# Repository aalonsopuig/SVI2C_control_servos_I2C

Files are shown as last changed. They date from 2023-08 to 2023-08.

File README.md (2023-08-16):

<html>

<head>
<meta http-equiv="Content-Language" content="es">
<meta name="GENERATOR" content="Microsoft FrontPage 4.0">
<meta name="ProgId" content="FrontPage.Editor.Document">
</head>

<font size="4"><b><i>Diseño de un módulo para control de
      8 servos y 5 canales analógicos por bus I<sup>2</sup>C</i></b></font>
      <p>Por Alejandro Alonso Puig<br>
      Octubre 2.003<br>
<hr>
<p align="justify"><br>
El presente repositorio incluye no solo los programas y esquemático del circuito en Eagle, 
sino también el informe técnico que describe el diseño, tanto desde el punto de vista
electrónico, como informático de un placa para control por bus I<sup>2</sup>C
de 8 servos estándar de radiocontrol y 5 entradas analógicas (Conversión
analógica/digital). Las características principales del módulo presentado son
las siguientes:&nbsp;</p>
<ul>
  <li>
    <p align="justify">Actúa como Slave permitiendo seleccionar mediante
    switches dip la dirección que utilizará en la red I<sup>2</sup>C.&nbsp;</li>
  <li>
    <p align="justify">Se puede establecer mediante bus I<sup>2</sup>C tanto la
    posición deseada de cada servo, como el sentido de giro y el Offset.&nbsp;</li>
  <li>
    <p align="justify">Se puede leer por bus I<sup>2</sup>C el valor digital (8
    bits) correspondiente a cualquiera de las 5 entradas analógicas de las que
    dispone.&nbsp;</li>
  <li>
    <p align="justify">Implementa un microcontrolador PIC 16F876 programado en ensamblador, lo que hace el código muy rápido.&nbsp;</li>
</ul>
<p align="justify">&nbsp;</p>
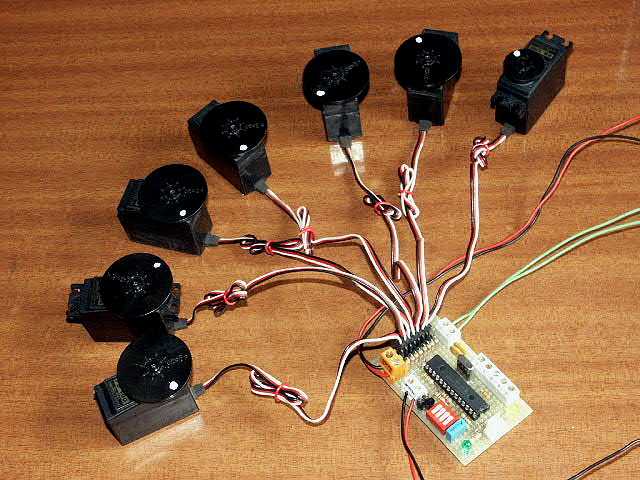
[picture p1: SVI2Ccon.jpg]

<p align="justify">La ventaja que se obtiene con este tipo de módulos es
precisamente el control por bus I<sup>2</sup>C que permite tener varios módulos
de este tipo ventaja que se obtiene con este tipo de módulos es precisamente el
control por bus I<sup>2</sup>C que permite tener varios módulos de este tipo
conectados al mismo bus. De esta manera pueden controlarse gran cantidad de
servos desde un controlador principal sin apenas sobrecarga en el mismo.
Adicionalmente se tiene medida de valores analógicos, muy útil para
determinado tipo de sensores.</p>
<p><b>Nota</b>: Master y Slave han de estar conectados mediante tres hilos:
Masa, SCL y SDA. El módulo presentado incluye las resistencias de PullUp, por
lo que no es necesario añadirlas.</p>
<p>

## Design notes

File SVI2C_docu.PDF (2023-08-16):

mundobot.com | Alejandro Alonso Puig

# Diseño de un módulo para control de 8 servos y 5 canales analógicos por bus I²

C

# Alejandro Alonso Puig – mundobot.com Octubre 2003

## Comandos I²

# Introducción

El siguiente informe técnico describe el diseño,

## tanto desde el punto de vista electrónico, como informático de un placa para control por bus I²

C

## de 8 servos estándar de radiocontrol y 5 entradas

analógicas (Conversión analógica/digital).

## Las características principales del módulo presentado son las siguientes:

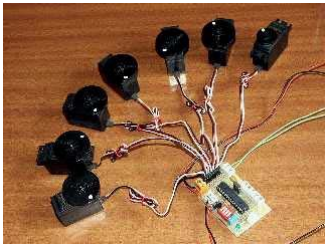
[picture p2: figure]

## - Actúa como Slave permitiendo seleccionar mediante switches dip la dirección que utilizará en la red I²

C.

## - Se puede establecer mediante bus I² C tanto la posición deseada de cada servo, como el

sentido de giro y el Offset.

## - Se puede leer por bus I² C el valor digital (8 bits) correspondiente a cualquiera de las 5

entradas analógicas de las que dispone..

## La ventaja que se obtiene con este tipo de módulos es precisamente el control por bus I²

C

## que permite tener varios módulos de este tipo

## conectados al mismo bus. De esta manera pueden controlarse gran cantidad de servos desde un controlador principal sin apenas sobrecarga en el mismo. Adicionalmente se tiene medida de valores analógicos, muy útil para determinado tipo de

sensores.

# Diseño Electrónico

## El módulo está compuesto básicamente por en un microcontrolador PIC 16F876 de Microchip

funcionando a 4Mhz.

## Este microcontrolador posee un módulo MSSP que permite el control de las comunicaciones I²

C

## por Hardware. Se utilizan los pines SCL (RC3) y SDA (RC4) conectados a resistencias Pull-Up de 10KΩ para las comunicaciones I²

C.

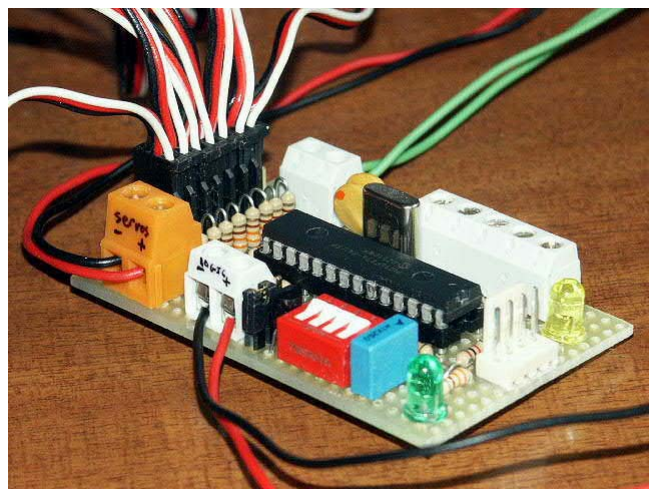
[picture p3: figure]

## Adicionalmente posee un grupo de cinco conversores analógico digitales (A/D) que pueden

soportar entradas analógicas entre 0 y 5 voltios.

## Los valores analógicos serán relativos a la masa del circuito, por lo que la masa del elemento cuya señal analógica se quiera medir deberá estar

conectada a la masa del modulo que presentamos.

## Existen 4 entradas (RB2-RB5) conectadas a un switch-dip cuádruple. Solo las dos inferiores (RB2, RB3) son utilizadas por el firmware actual

## y permitirán seleccionar diferentes direcciones

I

2

## C para evitar coincidencia de direccionamiento con otros dispositivos (entre 01110000 [0x70] y

01110110 [0x76]).

Tiene doble entrada de alimentación, una para los servos y otra para la lógica. Utilizar doble alimentación no es obligatorio, aunque si es recomendable para evitar interferencias en el funcionamiento de la lógica. En cualquier caso el módulo incluye un regulador de tensión a 5 voltios (7805) que puede ser activado o desactivado mediante jumper, según se vaya a

alimentar el circuito con 5 voltios o más.

## Obviamente la masa de ambas tomas de

alimentación es común.

## Finalmente los pines MCLR, RB6 y RB7 se han llevado junto con la masa a un conector cuádruple con el fin de permitir la programación del chip

una vez montado en placa (Programación ICP).

## Las salidas para el control del los servos incluyen resistencias de 330Ω para prevenir daños en el microcontrolador en caso de exceso de consumo

en el circuito interno de los servos.

## El circuito no está protegido en caso de conectar la alimentación incorrectamente, por lo que se ha

de prestar atención a la polaridad.

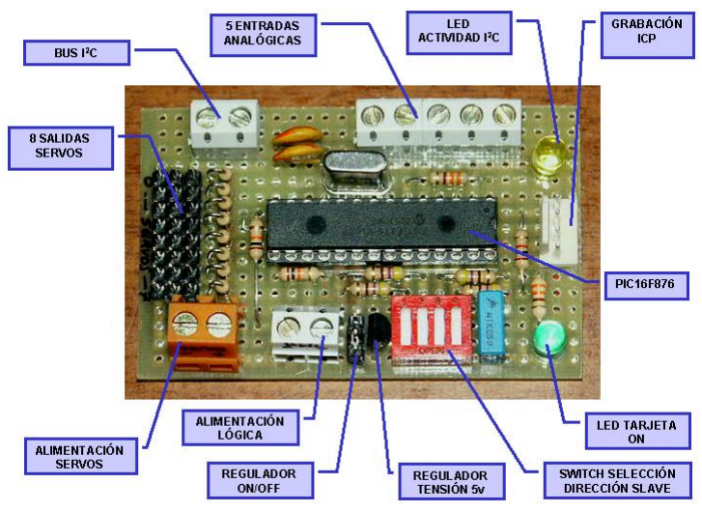
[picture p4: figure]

El esquema electrónico completo se muestra a continuación.

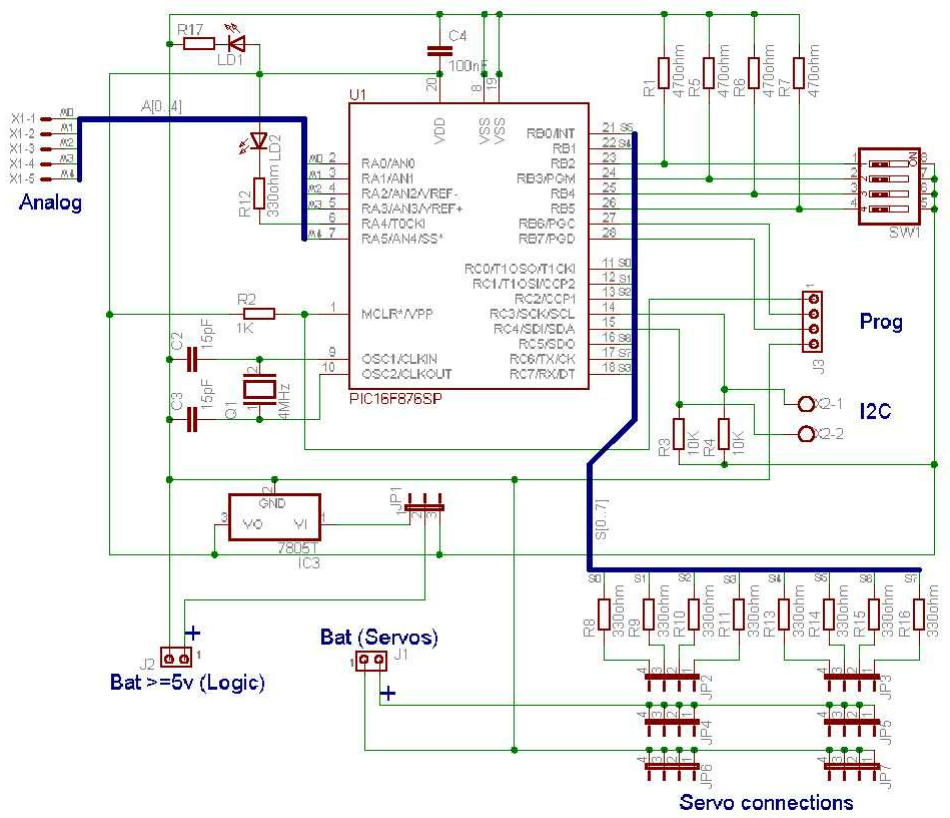
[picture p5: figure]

# Diseño del software

## El software ha sido desarrollado en ensamblador

para PIC16F876.

## El módulo está configurado para producir una interrupción cada vez que se desborda el timer TMR0 o cada vez que se produce un evento I²

C.

## Al atender dicha interrupción verifica cual de los dos tipos es y actúa en consecuencia:

## 9 El TMR0 se configura con un valor adecuado para que se desborde cada 20msg, que es el tiempo en el que se ha de refrescar el valor PWM enviado a los

servos. | Cuando | se | produce | una

## interrupción de este tipo, se atienden los 8 servos secuencialmente, vigilando asimismo si se produce simultáneamente un evento I² C. En caso de producirse, se forzará la parada de la señal de reloj I²

| | | | C

## para que el Master no envíe más información hasta que se tenga tiempo de atender el evento que ha llegado. Así se

impiden overflows.

## 9 Si el evento que ha producido la interrupción es I² C, se atenderá en la rutina “SSP_Handler”, que verificará la adecuada llegada de tramas y se ocupará de actualizar o leer una serie de registros de los que hablaremos más adelante y que serán los responsables del funcionamiento

del módulo.

# Registros

## El módulo contiene una serie de registros que pueden ser accedidos desde un Master por I²

| | | | C.
Algunos de estos registros son solo de lectura, mientras que otros son de escritura.

## Mediante el manejo de estos registros se obtiene toda la funcionalidad del módulo. A continuación describimos dichos registros:

## - Modo: Este registro permite al Master especificar el modo de funcionamiento de cada servo: Normal (giro normal) y Reverse (sentido inverso)

## Cada bit representa un servo. Así por ejemplo, si Modo es 10010100, los servos 0, 1, 3, 5 y 6 girarán en sentido normal y los servos 2, 4 y 7 funcionarán en sentido

inverso.

## Por defecto este registro vale 0, con lo que

todos los servos giran en sentido normal.

## - Offset: Es un registro de solo escritura cuyo valor por defecto es 70. Permite

ajustar la posición cero del servo. Es decir,

## debido a que cada modelo de servo tiene unas características diferentes, la posición cero de dos servos diferentes puede darse en diferentes Duty Cycles (Anchura del pulso positivo). Por ejemplo en un servo

se puede dar con un Duty Cycle de 1msg,

mientras que en otro se puede dar con un Duty Cycle de 400µsg. Por ello ha de ajustarse el Offset a las características del servo. Ha de tenerse en cuenta que una variación de una unidad en el Offset implica una variación de 5µsg en el Duty Cycle. Asimismo ha de tenerse en cuenta que el valor del Duty Cycle vendrá dado en µsg por la siguiente fórmula en este módulo:

## Duty Cycle = 10 + 5xOffset + 8xPosic

## De esta manera, para la posición 0, el Offset será:

5

## −10 = DutyCycle Offset

## Así, para un Duty Cycle de 1msg (1000µsg) en la posición 0, el Offset habrá de ser 198

## - Posic: Es un registro de solo escritura cuyo valor por defecto es 0. Indica la

posición que se desea que tenga el servo. El límite depende del modelo de servo.

Básicamente ha de tenerse en cuenta que un incremento de una unidad en este valor implica un incremento de 8 µsg en el Duty Cycle. Según el valor del Offset de un servo y del valor de Posic, se tendrá un Duty Cycle concreto según la fórmula que se mostró antes. Por ejemplo para un Offset de valor 70 (valor por defecto) y un valor de Posic de 220 generaría una señal

PWM de Duty Cycle = 2.120µsg.

## Por tanto se tiene que los valores límites de Duty Cycle que se pueden conseguir con este módulo varían desde 10µsg

(Offset=0, | Posic=0) | a | 3.325µsg

## (Offset=255, Posic=255)

Los valores son muy extremos, por lo que hay que tener cuidado en su asignación para no dañar el servo. En caso de no conocerse los límites de Duty Cycle de un servo puede procederse de la siguiente manera: Establecer para un servo concreto desde el Master un valor de Posic=0 y un Offset=198. Esto generará un PWM de Duty Cycle = 1000µsg, valor aceptado por cualquier servo comercial. Si se observa que el eje del servo está lejos de su posición de límite físico, se irá reduciendo el valor del Duty Cycle hasta que el eje esté cerca del límite físico. No ha de llegar en ningún momento al límite físico ya que podría dañar el mecanismo de engranajes del servo. Una vez establecido el valor de Offset, se puede ir incrementando progresivamente el valor de Posic hasta que el eje casi llegue a su otro límite físico. Con esto ya se ha conseguido saber

## el valor que ha de tener Offset y los valores límites de Posic

- Analog: Es un registro de solo lectura.

## Indica el valor digital de la conversión A/D de una entrada analógica concreta. La resolución usada en la conversión A/D es de 8 bits, es decir que lo mínimo

detectable son variaciones de 19,5mV.

- Versión: Indica la versión del firmware. Es un registro de solo lectura.

# Comandos I²

C

## Básicamente las órdenes que llegarán del Master al Slave serán de lectura y/o escritura en los

registros mencionados anteriormente.

## En la primera trama se indica el número de registro al que se quiere acceder, bien sea para lectura o escritura. Dicha numeración es la siguiente:

## 1. Registro de Modo 2. Offset servo 3. Posición servo 4. Conversor A/D 5. No usado 6. No usado

7. Revisión Firmware.

## En la segunda trama se indica el número de dispositivo al que nos referimos (número de servo o número de entrada analógica)

## Si estamos escribiendo un registro, en la tercera trama irá el valor que escribimos. Si por el contrario estamos accediendo en modo lectura, se

enviará orden de solicitud del valor del registro.

## Por ejemplo, si se quiere ordenar que el servo número 0 tenga un Offset de 92, habría que enviar un bloque con cuatro bytes:

## 9 Dirección Slave en modo escritura (si no se cambian los switches será 112

(01110000))

## 9 Nº Registro a acceder (Offset=2) 9 Nº Dispositivo a acceder (Servo0 --> 0) 9 Valor Registro: 92

## Si lo que se quiere por ejemplo es leer el valor de la entrada analógica número 3, se enviaría un primer bloque con 3 bytes:

## 9 Dirección Slave en modo escritura (si no se cambian los switches será 112

(01110000))

## 9 Nº Registro a acceder (A/D=4) 9 Nº Dispositivo a acceder (Entrada nº 3 -->

3)

## Tras esto se enviaría un segundo bloque con un byte:

## 9 Dirección Slave en modo lectura (si no se

cambian | los | switches | será | 113
(01110001))

## .. y se recibirá del Slave un byte correspondiente

al dato solicitado.

## A continuación se muestra el formato de los comandos I² C utilizados para el intercambio de datos entre Master y Slave a nivel de lógica

digital.

## Escritura registro

## En caso de querer escribir en un registro, se enviará desde el Master al Slave un solo bloque de datos con cuatro bytes (Dirección Slave en modo escritura, nº registro, nº dispositivo, valor

registro).

## Tomando el ejemplo anterior de establecimiento de un valor 92 para el Offset, la representación de la transmisión a nivel de lógica digital sería como sigue:

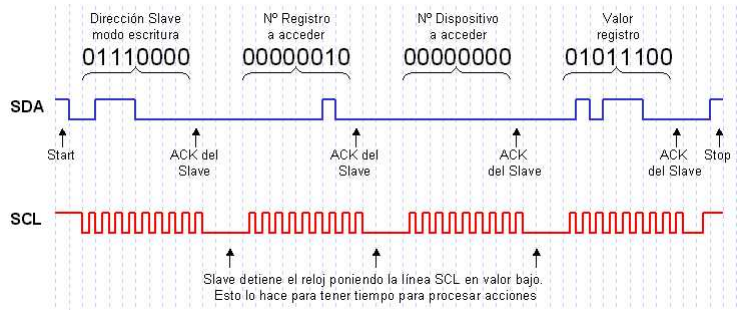
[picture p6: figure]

## Lectura Registro

## En caso de querer leer de un registro, se enviará desde el Master al Slave un bloque con tres bytes (Dirección Slave en modo escritura, nº registro, nº dispositivo) y otro bloque con un byte (Dirección

## Slave en modo lectura). El Slave contestará con otro bloque de un byte (valor de registro solicitado)

## Tomando el ejemplo anterior de lectura de un valor del conversor A/D, la representación de la

## transmisión a nivel de lógica digital sería como sigue:

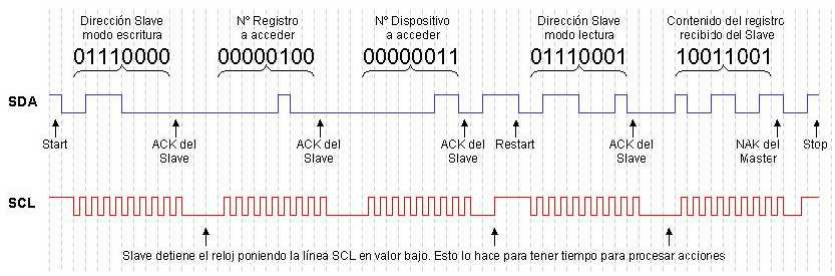
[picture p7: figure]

# Cuerpo del programa

Básicamente el funcionamiento del programa consiste en un bucle en el que mientras no se produzca una interrupción por evento I² C o por desbordamiento del TMR0, Va haciendo conversiones A/D de sus 5 entradas analógicas y dejándolas en variables para que en caso de ser solicitadas por I² C pueda entregar los valores de

## forma inmediata. Esto se hace porque la toma de un valor analógico y su conversión a un dato digital toma cierto tiempo. Teniendo siempre los

valores ya convertidos, se agiliza la transmisión.

# Código fuente

A continuación se incluye el código fuente del módulo comentado. Incluye comentarios que aclararán su funcionamiento.

; SvI2C02
; Programa para control de servos y entradas analógicas por bus I2C ; Por: Alejandro Alonso Puig
; Fecha: 11/10/2003
; Controlador: 16F876 4Mhz
; Función:
; Control de hasta 8 servos y 5 entradas analógicas.
; Dispone de las siguientes características:
; -Valores de posicionamiento (0 a 255)
; -Permite funcionar a cada servo en modo normal o reverse
; -Permite establecer un Offset por servo para fijar posición inicial ; -Switches dip para especificar la dirección i2c que se utilizará
; -Conversión A/D de 5 entradas analógicas
;

; La anchura de flanco alto (Duty Cycle) enviada a cada servo vendrá dada en usg por la formula ; Duty Cycle en usg = 10 + 5xOffset + 8xPosic en caso de funcionamiento normal y
; Duty Cycle en usg = 10 + 5xOffset + 8x(255-Posic) en caso de funcionamiento reverse
list | p=16F876
include | "P16F876.INC"

;Definición de macros

#define Version | d'02' | ;Versión del programa

;Puertos
#define Servo0 PORTC,0 | ; Servo nº0

#define Servo1 PORTC,1 | ; Servo nº1

#define Servo2 PORTC,2 | ; Servo nº2

#define Servo3 PORTC,7 | ; Servo nº3

#define Servo4 PORTB,1 | ; Servo nº4

#define Servo5 PORTB,0 | ; Servo nº5

#define Servo6 PORTC,5 | ; Servo nº6

#define Servo7 PORTC,6 | ; Servo nº7

#define S0 | .0 | ;Referencia al servo 0 en palabras de estado

#define S1 | .1 | ;Referencia al servo 1 en palabras de estado

#define S2 | .2 | ;Referencia al servo 2 en palabras de estado

#define S3 | .3 | ;Referencia al servo 3 en palabras de estado

#define S4 | .4 | ;Referencia al servo 4 en palabras de estado

#define S5 | .5 | ;Referencia al servo 5 en palabras de estado

#define S6 | .6 | ;Referencia al servo 6 en palabras de estado

#define S7 | .7 | ;Referencia al servo 7 en palabras de estado

#define Led | PORTA,4 | ;Led de actividad I2C

;Definición de variables

cblock 0x20

;Variables para control de servos
DispNo | ;Numero de dispositivo accedido desde I2C (Servo, pto Analog)
Posic | ;Variable Posicion Servo para cálculo retardo
Posic0 | ;Posicion Servo nº0 (0 a 255)
Posic1 | ;Posicion Servo nº1 (0 a 255)
Posic2 | ;Posicion Servo nº2 (0 a 255)
Posic3 | ;Posicion Servo nº3 (0 a 255)
Posic4 | ;Posicion Servo nº4 (0 a 255)
Posic5 | ;Posicion Servo nº5 (0 a 255)
Posic6 | ;Posicion Servo nº6 (0 a 255)
Posic7 | ;Posicion Servo nº7 (0 a 255)

;Offsets
;El valor de Offset permite establecer la posición inicial de cada en función ;de la anchura del pulso activo en microsegundos. El cálculo se hace mediante ;la fórmula Offset=(T-10)/5, donde T es la anchura del pulso activo en usg ;Se utiliza para dos funciones: Ajustar varios servos para que sus ejes estén ;colocados físicamente en la misma posición cero, adaptando los
;offsets de cada servo. También se utiliza para aprovechar al máximo el giro ;posible del eje, que varia para cada marca y modelo.
;Por ejemplo, si queremos establecer que el valor de 0 implique un pulso ;activo de una anchura de 1000usg, el offset será (1000-10)/5=198
Offset0 | ;Offset Servo nº0
Offset1 | ;Offset Servo nº1
Offset2 | ;Offset Servo nº2
Offset3 | ;Offset Servo nº3
Offset4 | ;Offset Servo nº4
Offset5 | ;Offset Servo nº5
Offset6 | ;Offset Servo nº6
Offset7 | ;Offset Servo nº7
Offset | ;Valor Offset servo
Modo | ;Palabra de estado que indica en cada bit que servo girará a la inversa
APort | ;Puerto analógico a medir
APortTmp | ;Variable temporal utilizada en la medición
Analog | ;Valor analógico medido

Analog0 | ;Valor analógico puerto 0
Analog1 | ;Valor analógico puerto 1
Analog2 | ;Valor analógico puerto 2
Analog3 | ;Valor analógico puerto 3
Analog4 | ;Valor analógico puerto 4
PDel0 | ;Usada en retardos
ADel0 | ;Usada en retardos
BDel0 | ;Usada en retardos
BDel1 | ;Usada en retardos
BDel2 | ;Usada en retardos
Pausa | ;Usada en para hacer pausas con subr "HacerTiempo"
Temp | ;Variable Temporal para usos puntuales en cálculos
Temp2 | ;Variable Temporal para usos puntuales en cálculos
Temp3 | ;Variable Temporal para usos puntuales en cálculos
BkStatus | ;Backup del registro STATUS
BkW | ;Backup W
BkStatus2 | ;Backup del registro STATUS (Interrupciones)
BkW2 | ;Backup W (Interrupciones)
DirNodo | ;Dirección I2C de este slave (4 posibles direcciones segun switches dip)
MensajeIn | ;Contendrá el dato recibido por I2C del master
MensajeOut | ;Contendrá el dato a enviar por I2C al master
Registro | ;Registro accedido por i2c:
; | 1: Registro de Modo. Normal o Reverse servo
; | 2: Offset servo
; | 3: Posición servo
; | 4: Valor puerto analógico
; | 5: No usado
; | 6: No usado
; | 7: Revisión Firmware. "Version"
StatI2C | ;Registro intermedio para identificar el estado i2c:
; | 0: Si On --> llegó nº Registro
; | 1: Si On --> llegó nº Dispositivo al que se referirá el registro
endc | ;Fin de definiciones
org | 0
goto | INICIO
org | 5

;-------------------------------------------------------------------------------
Interrupcion | ;RUTINA DE INTERRUPCIÓN. Activa flancos segun valor de variables
| ;de Posicion (Servos) y trata eventos I2C
;-------------------------------------------------------------------------------

;Guardamos copia de algunos registros
movwf | BkW2 | ;Hace copia de W
movf | STATUS,W | ;Hace copia de registro de estado
banksel BkStatus2
movwf BkStatus2

;Chequeamos si la interrupción es por evento I2C. En caso positivo llamamos ;a la rutina de proceso del evento
banksel PIR1
btfss | PIR1,SSPIF | ;Ha ocurrido un evento SSP? (I2C)
goto | IntNoSSP | ;No. entonces será por otra cosa. Saltamos.
bcf | SSPCON,CKP | ;Si. Detenemos reloj I2C para evitar desbordamiento o timeout
banksel PORTA
bcf | Led | ;Enciende led de actividad I2C
call | SSP_Handler | ;Procesamos el evento.
banksel PIR1
bcf | PIR1,SSPIF | ;Limpiamos el flag
goto | Rest
IntNoSSP | ;Aquí se gestionan interrupciones que no son por SSP

;Es una interrupción de desbordamiento del TMR0 --> Gestión Servos

| bcf | INTCON,T0IF | ;Repone flag del TMR0
| movlw | d'177' | ;Repone el TMR0 con 177 (complemento de 78) -182
banksel TMR0
movwf TMR0 | ;256*78=19.968 (casi 20.000 usg= 20ms)

;** SERVO0 **
| movlw | d'255' | ;Precargamos Posic con 255...
| movwf | Posic | ;...por si ha de funcionar en reverse mode
| movf | Posic0,W | ;Carga variable Posic con valor posición para servo
| btfsc | Modo,S0 | ;Verifica si ha de funcionar en reverse mode
| goto | Inv0 | ;Si. invertimos valor
| movwf | Posic | ;No
| goto | Sigue0
Inv0 | subwf | Posic,F | ;Si. invertimos valor
Sigue0 movf | Offset0,w | ;Carga Offset del servo correspondiente
| movwf | Offset
| bsf | Servo0 | ;activamos flanco
| call | Retardo | ;dejamos activo el tiempo necesario
| bcf | Servo0 | ;bajamos flanco

;** SERVO1 **
| movlw | d'255' | ;Precargamos Posic con 255...
| movwf | Posic | ;...por si ha de funcionar en reverse mode
| movf | Posic1,W | ;Carga variable Posic con valor posición para servo
| btfsc | Modo,S1 | ;Verifica si ha de funcionar en reverse mode
| goto | Inv1 | ;Si. invertimos valor
| movwf | Posic | ;No
| goto | Sigue1
Inv1 | subwf | Posic,F | ;Si. invertimos valor
Sigue1 movf | Offset1,w | ;Carga Offset del servo correspondiente
| movwf | Offset
| bsf | Servo1 | ;activamos flanco
| call | Retardo | ;dejamos activo el tiempo necesario
| bcf | Servo1 | ;bajamos flanco

;** SERVO2 **
| movlw | d'255' | ;Precargamos Posic con 255...
| movwf | Posic | ;...por si ha de funcionar en reverse mode
| movf | Posic2,W | ;Carga variable Posic con valor posición para servo
| btfsc | Modo,S2 | ;Verifica si ha de funcionar en reverse mode
| goto | Inv2 | ;Si. invertimos valor
| movwf | Posic | ;No
| goto | Sigue2
Inv2 | subwf | Posic,F | ;Si. invertimos valor
Sigue2 movf | Offset2,w | ;Carga Offset del servo correspondiente
| movwf | Offset
| bsf | Servo2 | ;activamos flanco
| call | Retardo | ;dejamos activo el tiempo necesario
| bcf | Servo2 | ;bajamos flanco

;** SERVO3 **
| movlw | d'255' | ;Precargamos Posic con 255...
| movwf | Posic | ;...por si ha de funcionar en reverse mode
| movf | Posic3,W | ;Carga variable Posic con valor posición para servo
| btfsc | Modo,S3 | ;Verifica si ha de funcionar en reverse mode
| goto | Inv3 | ;Si. invertimos valor
| movwf | Posic | ;No
| goto | Sigue3
Inv3 | subwf | Posic,F | ;Si. invertimos valor
Sigue3 movf | Offset3,w | ;Carga Offset del servo correspondiente
| movwf | Offset
| bsf | Servo3 | ;activamos flanco
| call | Retardo | ;dejamos activo el tiempo necesario
| bcf | Servo3 | ;bajamos flanco

;** SERVO4 **
| movlw | d'255' | ;Precargamos Posic con 255...
| movwf | Posic | ;...por si ha de funcionar en reverse mode
| movf | Posic4,W | ;Carga variable Posic con valor posición para servo
| btfsc | Modo,S4 | ;Verifica si ha de funcionar en reverse mode
| goto | Inv4 | ;Si. invertimos valor
| movwf | Posic | ;No
| goto | Sigue4
Inv4 | subwf | Posic,F | ;Si. invertimos valor

Sigue4 movf | Offset4,w | ;Carga Offset del servo correspondiente
| movwf | Offset
| bsf | Servo4 | ;activamos flanco
| call | Retardo | ;dejamos activo el tiempo necesario
| bcf | Servo4 | ;bajamos flanco

;** SERVO5 **
| movlw | d'255' | ;Precargamos Posic con 255...
| movwf | Posic | ;...por si ha de funcionar en reverse mode
| movf | Posic5,W | ;Carga variable Posic con valor posición para servo
| btfsc | Modo,S5 | ;Verifica si ha de funcionar en reverse mode
| goto | Inv5 | ;Si. invertimos valor
| movwf | Posic | ;No
| goto | Sigue5
Inv5 | subwf | Posic,F | ;Si. invertimos valor
Sigue5 movf | Offset5,w | ;Carga Offset del servo correspondiente
| movwf | Offset
| bsf | Servo5 | ;activamos flanco
| call | Retardo | ;dejamos activo el tiempo necesario
| bcf | Servo5 | ;bajamos flanco

;** SERVO6 **
| movlw | d'255' | ;Precargamos Posic con 255...
| movwf | Posic | ;...por si ha de funcionar en reverse mode
| movf | Posic6,W | ;Carga variable Posic con valor posición para servo
| btfsc | Modo,S6 | ;Verifica si ha de funcionar en reverse mode
| goto | Inv6 | ;Si. invertimos valor
| movwf | Posic | ;No
| goto | Sigue6
Inv6 | subwf | Posic,F | ;Si. invertimos valor
Sigue6 movf | Offset6,w | ;Carga Offset del servo correspondiente
| movwf | Offset
| bsf | Servo6 | ;activamos flanco
| call | Retardo | ;dejamos activo el tiempo necesario
| bcf | Servo6 | ;bajamos flanco

;** SERVO7 **
| movlw | d'255' | ;Precargamos Posic con 255...
| movwf | Posic | ;...por si ha de funcionar en reverse mode
| movf | Posic7,W | ;Carga variable Posic con valor posición para servo
| btfsc | Modo,S7 | ;Verifica si ha de funcionar en reverse mode
| goto | Inv7 | ;Si. invertimos valor
| movwf | Posic | ;No
| goto | Sigue7
Inv7 | subwf | Posic,F | ;Si. invertimos valor
Sigue7 movf | Offset7,w | ;Carga Offset del servo correspondiente
| movwf | Offset
| bsf | Servo7 | ;activamos flanco
| call | Retardo | ;dejamos activo el tiempo necesario
| bcf | Servo7 | ;bajamos flanco
Rest | bsf | SSPCON,CKP | ;Activamos reloj I2C
banksel PORTA
| bsf | Led | ;apaga led de actividad I2C

;Restauramos las copias de los registros
banksel BkStatus2
| movf | BkStatus2,W | ;Restaura las copias de registros
| movwf | STATUS | ;registro de estado
| movf | BkW2,W | ;registro W
| retfie

; ---------------------------------------------------------------------------------------

INICIO | ;Inicio del cuerpo del programa

banksel TRISA
movlw | b'00101111' | ;A0,1,2,3,5 Entradas (Analógicas) , A4 Salida (Led)
movwf | TRISA | ;
movlw | b'00111100' | ;B0,B1 Salida (Servos), B2,B3,B4,B5 switches dip. B6,B7 prog

movwf | TRISB | ;
movlw | b'00000000' | ;C0,C1,C2,C5,C6,C7 Salida (Servos). C3,C4 I2C
movwf | TRISC | ;

;Configuración para interrupciones por overflow de TMR0

banksel OPTION_REG
movlw | b'10000111' | ;Configuracion OPTION para TMR0 (Prescaler 1:256)
movwf | OPTION_REG
movlw | b'10100000' | ;Establece interrupciones
movwf | INTCON | ;activas para overflow de TMR0
bcf | INTCON,GIE | ;..pero no la general de momento
banksel TMR0
movlw | d'177' | ;Activa el TMR0 con 177 (complemento de 78)
movwf TMR0 | ;256*78=19.968 (casi 20.000 usg= 20ms)

;Configuración para gestión i2c
call init_i2c_Slave ;Configuración para uso de i2c
banksel INTCON
bsf | INTCON,GIE | ;Activamos las interrupciones

banksel Posic1

;Posiciones por defecto de los servos
clrf | Posic0
clrf | Posic1
clrf | Posic2
clrf | Posic3
clrf | Posic4
clrf | Posic5
clrf | Posic6
clrf | Posic7

;Valores por defecto de los Offsets
movlw | d'70'
movwf | Offset0
movwf | Offset1
movwf | Offset2
movwf | Offset3
movwf | Offset4
movwf | Offset5
movwf | Offset6
movwf | Offset7

;En Principio todos los servos funcionaran sin reverse mode
clrf | Modo
clrf | StatI2C

;Todas las entradas analógicas están a 0
clrf | PORTA
clrf | APort
clrf | Analog
clrf | Analog0
clrf | Analog1
clrf | Analog2
clrf | Analog3
clrf | Analog4

BUCLE

;Leemos puerto analógico 0 banksel APort
clrf | APort
call | ReadAnalog
movf | Analog,W
movwf | Analog0

;Leemos puerto analógico 1
incf | APort,F
call | ReadAnalog
movf | Analog,W

movwf Analog1

;Leemos puerto analógico 2
incf | APort,F
call | ReadAnalog
movf | Analog,W
movwf | Analog2

;Leemos puerto analógico 3
incf | APort,F
call | ReadAnalog
movf | Analog,W
movwf | Analog3

;Leemos puerto analógico 4
incf | APort,F
call | ReadAnalog
movf | Analog,W
movwf | Analog4

goto BUCLE

;********************************************************************************* ; SUBRUTINAS
;*********************************************************************************

; ---------------------------------------------------------------------------------------
Retardo | ;Provoca un retardo segun el valor de "Posic" y "Offset". Su valor en
;usg será: Retardo = 10 + 5xOffset + 8xPosic ; ---------------------------------------------------------------------------------------

;Chequeo inicial: Delay fijo de 4usg (4 ciclos)
;-------------
movf | Posic,F | ;Checkeamos si el valor es cero
btfsc | STATUS,Z | ;
goto | DelFijo | ;Si es cero salta a la parte de delay fijo
NOP

;Primera parte: Delay variable en función Posic (entre 0 y 255). Ciclos=Posic x 8 ;--------------

PLoop0 btfsc PIR1,SSPIF | ; Ha ocurrido un evento SSP? (I2C)
bcf | SSPCON,CKP | ; Si. Detenemos reloj I2C para evitar desbordamiento o timeout
NOP
NOP
NOP
decfsz Posic,F | ; 1 + (1) es el tiempo 0 ?
goto | PLoop0 | ; 2 no, loop
NOP

;Segunda parte: Delay fijo dependiente del valor de Offset. Ciclos=6+5xOffset ;-------------

DelFijo
movf | Offset,W | ; 1 set numero de repeticion
movwf PDel0 | ; 1 |
SLoop0 btfsc PIR1,SSPIF | ; Ha ocurrido un evento SSP? (I2C)
bcf | SSPCON,CKP | ; Si. Detenemos reloj I2C para evitar desbordamiento o timeout
decfsz PDel0, 1 | ; 1 + (1) es el tiempo 0 ?
goto | SLoop0 | ; 2 no, loop
return | | ; 2+2 Fin.

;-------------------------------------------------------------------------------
init_i2c_Slave | ;Inicializa valores para uso de I2C en Slave

;Ha de ser llamado tras definir TRISC (de ser necesario) ;-------------------------------------------------------------------------------

;Guardamos copia de algunos registros
movwf | BkW | ;Hace copia de W
movf | STATUS,W | ;Hace copia de registro de estado
banksel BkStatus
movwf BkStatus

;Establecemos dirección del esclavo segun switches dip (B2 y B3)
movlw | b'01110000'
movwf | DirNodo
btfsc | PORTB,2
bsf | DirNodo,2
btfsc | PORTB,3
bsf | DirNodo,1

;Configuramos I2C
banksel TRISC | ; Pasamos a direccionar Banco 1
movlw | b'00011000' | ; Establece líneas SDA y SCL como entradas...
iorwf | TRISC,F | ;..respetando los valores para otras líneas.
bcf | SSPSTAT,CKE | ; Establece I2C input levels
bcf | SSPSTAT,SMP | ; Habilita slew rate
bsf | SSPCON2,GCEN | ; Habilita direccionamiento global
banksel DirNodo
movf | DirNodo,W | ; Dirección esclavo
banksel SSPADD
movwf | SSPADD | ;
banksel SSPCON | ; Pasamos a direccionar Banco 0
movlw | b'00110110' | ; Slave mode, SSP enable,
movwf | SSPCON | ;
bcf | PIR1,SSPIF | ; Limpia flag de eventos SSP
bcf | PIR1,7 | ; Limpia bit. Mandatorio por Datasheet

;Configuración para interrupciones por evento I2C
banksel PIE1
bsf | PIE1,SSPIE
bsf | INTCON,PEIE

;Restauramos las copias de los registros
movf | BkStatus,W | ;Restaura las copias de registros
movwf | STATUS | ;registro de estado
movf | BkW,W | ;registro W

return

; --------------------------------------------------------------------------------------SSP_Handler ; Este manejador controla cada evento SSP (I2C) acontecido.
; El código que se muestra abajo chequea 5 posibles estados. ; Cada uno de los 5 estados SSP son identificados haciendo
; XOR de los bits del registro SSPSTAT con mascaras de bits ; predeterminadas. Una vez que el estado ha sido identificado
; se llevan a cabo las acciones pertinentes. Los estados
; indefinidos son considerados como estados de error.

; State 1: Operación de escritura I2C, ultimo byte era de dirección. ; SSPSTAT bits: S = 1, D_A = 0, R_W = 0, BF = 1

; State 2: Operación de escritura I2C, ultimo byte era de datos.
; SSPSTAT bits: S = 1, D_A = 1, R_W = 0, BF = 1

; State 3: Operación de lectura I2C, ultimo byte era de dirección. ; SSPSTAT bits: S = 1, D_A = 0, R_W = 1, BF = 0

; State 4: Operación de lectura I2C, ultimo byte era de datos.
; SSPSTAT bits: S = 1, D_A = 1, R_W = 1, BF = 0

; State 5: Reset lógico del Slave I2C por NACK del master.
; SSPSTAT bits: S = 1, D_A = 1, R_W = 0, BF = 0

; --------------------------------------------------------------------------------------

banksel SSPSTAT
movf | SSPSTAT,W | ; Obtiene el valor de SSPSTAT

andlw | b'00101101' | ; elimina los bits no importantes SSPSTAT.
banksel Temp
movwf | Temp | ; para chequeo posterior.
State1: | ; Operación de escritura, ultimo byte ha sido
movlw | b'00001001' | ; de dirección, el buffer está lleno.
banksel Temp
xorwf | Temp,W | ;
btfss | STATUS,Z | ; Estamos en el primer estado?
goto | State2 | ; No, checkeamos siguiente estado
call | ReadI2C | ; SI. Hacemos un read SSPBUF (para vaciar buffer).
bcf | StatI2C,0 | ; Limpiamos flags de control de ...
bcf | StatI2C,1 | ; ...llegada de tramas
| | ; El Hardware se ocupa de mandar Ack
return
State2: | ; Operación de escritura, ultimo byte ha sido
movlw | b'00101001' | ; de datos, el buffer está lleno.
banksel Temp
xorwf | Temp,W
btfss | STATUS,Z | ; Estamos en el segundo estado?
goto | State3 | ; NO, checkeamos siguiente estado
call | ReadI2C | ; SI, Tomamos el byte del SSP.

;Aquí tenemos en W el valor del dato recibido
movwf | MensajeIn
btfsc | StatI2C,0 | ;Chequeamos que dato es (registro, nºdispositivo o valor)
goto | RegYaLlego | ;Registro ya llegó así que es nºservo o valor
movf | MensajeIn,W | ;Es Registro
movwf | Registro
bsf | StatI2C,0
return

RegYaLlego
btfsc | StatI2C,1 | ;Chequeamos que dato es (nºdispositivo o valor)
goto | DisYaLlego | ;nºdispositivo ya llegó así que es valor
movf | MensajeIn,W | ;Es nºdispositivo
movwf | DispNo
bsf | StatI2C,1
return
DisYaLlego | ;Sabemos el registro, nºdispositivo y tenemos el dato, actualizamos dato del registro
call | UpdateReg
return
State3: | ; Operación de lectura, ultimo byte ha sido
movlw | b'00001100' | ; de dirección, el buffer está vacío
banksel Temp
xorwf | Temp,W
btfss | STATUS,Z | ; Estamos en el tercer estado?
goto | State4 | ; NO, checkeamos siguiente estado
| | ; SI
btfsc | StatI2C,0 | ;Chequeamos si ya sabemos el registro a leer
goto | RegYaLlegoR | ;Lo sabemos,
movlw | 0 | ;No lo sabemos, devolvemos un cero por defecto
call | WriteI2C | ;escribimos el byte en SSPBUF
return
RegYaLlegoR
btfsc | StatI2C,1 | ;Chequeamos si ya sabemos el nºdispositivo a leer
goto | DisYaLlegoR | ;Lo sabemos
movlw | 0 | ;No lo sabemos, devolvemos un cero por defecto
call | WriteI2C | ;escribimos el byte en SSPBUF
return
DisYaLlegoR | ;Sabemos el registro y nºdispositivo a leer. Lo leemos y enviamos el dato
call | ReadReg
movf | MensajeOut,W
call | WriteI2C | ; SI, escribimos el byte en SSPBUF
bcf | StatI2C,0 | ; Limpiamos flags de control de ...
bcf | StatI2C,1 | ; ...llegada de tramas
return
State4: | ; Operación de lectura, ultimo byte ha sido
movlw | b'00101100' | ; de datos, el buffer está vacío
banksel Temp
xorwf Temp,W

btfss | STATUS,Z | ; Estamos en el cuarto estado?
goto | State5 | ; NO, checkeamos siguiente estado
| | ; SI. Operación no admitida.
movlw | 0 | ; devolvemos un cero por defecto
call | WriteI2C | ; escribimos el byte en SSPBUF
return

State5:
movlw | b'00101000' | ; Se ha recibido un NACK mientras se transmitían...
banksel Temp
xorwf | Temp,W | ; ..datos al master. La lógica del Slave..
btfss | STATUS,Z | ; ..se resetea en este caso. R_W = 0, D_A = 1
goto | I2CErr | ; y BF = 0
return | | ; Si no estamos en State5, entonces es
| | ; que algo fue mal
I2CErr nop | | ; Algo fue mal. Reseteamos el módulo I2C
call | ReadI2C | ; Vaciamos buffer por si hubo overflow
banksel SSPCON
bcf | SSPCON,SSPEN | ; Detenemos I2C
banksel SSPSTAT
clrf | SSPSTAT
bcf | SSPSTAT,CKE | ; Establece I2C input levels
bcf | SSPSTAT,SMP | ; Habilita slew rate
banksel SSPCON
bsf | SSPCON,SSPEN | ; Reactivamos I2C

return

;---------------------------------------------------------------------
WriteI2C | ;Usada por SSP_Handler para escribir datos en bus I2C
;---------------------------------------------------------------------

banksel SSPCON
movwf | SSPBUF | ; Escribe el dato en W
bsf | SSPCON,CKP | ; Libera el reloj
return

;---------------------------------------------------------------------
ReadI2C | ;Usada por SSP_Handler para escribir datos en bus I2C
;---------------------------------------------------------------------

banksel SSPBUF
movf | SSPBUF,W | ; Toma el byte y lo guarda en W
return

;---------------------------------------------------------------------
UpdateReg | ;Actualiza Registro ordenado por I2C
;---------------------------------------------------------------------

;Procedemos a actuar según la orden recibida del Master. Haremos un Pseudo CASE ;que actualice solo los registros escribibles e ignore los que no se puedan escribir

M_01 | ;xxxxxxxxx Modo xxxxxxxxx
movlw | d'1' | ;
xorwf | Registro,W | ;
btfss | STATUS,Z | ; Es este el registro a actualizar?
goto | M_02 | ; No, chequeamos siguiente caso
movf | MensajeIn,W | ; Si. procedemos a actualizar el registro
movwf | Modo
return | ;Regresamos a la espera de una nueva orden
M_02 | ;xxxxxxxxx Offset xxxxxxxxx
movlw | d'2' | ;
xorwf | Registro,W | ;
btfss | STATUS,Z | ; Es este el registro a actualizar?
goto | M_03 | ; No, chequeamos siguiente caso
; Si. procedemos a actualizar registro del servo correspondiente
O_00 | movlw | d'0'
xorwf | DispNo,W
btfss | STATUS,Z | ; Es este el servo a actualizar?

goto | O_01 | ; No, chequeamos siguiente caso
movf | MensajeIn,W | ; Si, actualizamos su registro
movwf | Offset0
return | ;Regresamos a la espera de una nueva orden
O_01 | movlw | d'1'
xorwf | DispNo,W
btfss | STATUS,Z | ; Es este el servo a actualizar?
goto | O_02 | ; No, chequeamos siguiente caso
movf | MensajeIn,W | ; Si, actualizamos su registro
movwf | Offset1
return | ;Regresamos a la espera de una nueva orden
O_02 | movlw | d'2'
xorwf | DispNo,W
btfss | STATUS,Z | ; Es este el servo a actualizar?
goto | O_03 | ; No, chequeamos siguiente caso
movf | MensajeIn,W | ; Si, actualizamos su registro
movwf | Offset2
return | ;Regresamos a la espera de una nueva orden
O_03 | movlw | d'3'
xorwf | DispNo,W
btfss | STATUS,Z | ; Es este el servo a actualizar?
goto | O_04 | ; No, chequeamos siguiente caso
movf | MensajeIn,W | ; Si, actualizamos su registro
movwf | Offset3
return | ;Regresamos a la espera de una nueva orden
O_04 | movlw | d'4'
xorwf | DispNo,W
btfss | STATUS,Z | ; Es este el servo a actualizar?
goto | O_05 | ; No, chequeamos siguiente caso
movf | MensajeIn,W | ; Si, actualizamos su registro
movwf | Offset4
return | ;Regresamos a la espera de una nueva orden
O_05 | movlw | d'5'
xorwf | DispNo,W
btfss | STATUS,Z | ; Es este el servo a actualizar?
goto | O_06 | ; No, chequeamos siguiente caso
movf | MensajeIn,W | ; Si, actualizamos su registro
movwf | Offset5
return | ;Regresamos a la espera de una nueva orden
O_06 | movlw | d'6'
xorwf | DispNo,W
btfss | STATUS,Z | ; Es este el servo a actualizar?
goto | O_07 | ; No, chequeamos siguiente caso
movf | MensajeIn,W | ; Si, actualizamos su registro
movwf | Offset6
return | ;Regresamos a la espera de una nueva orden
O_07 | movlw | d'7'
xorwf | DispNo,W
btfss | STATUS,Z | ; Es este el servo a actualizar?
goto | O_Err | ; No, chequeamos siguiente caso
movf | MensajeIn,W | ; Si, actualizamos su registro
movwf | Offset7
return | ;Regresamos a la espera de una nueva orden
O_Err | return | ;Error en numero de servo. No se hace nada
M_03 | ;xxxxxxxxx Posicion xxxxxxxxx
movlw | d'3' | ;
xorwf | Registro,W | ;
btfss | STATUS,Z | ; Es este el registro a actualizar?
goto | M_Error | ; No, chequeamos siguiente caso
; Si. procedemos a actualizar registro del servo correspondiente
S_00b | movlw | d'0'
xorwf | DispNo,W
btfss | STATUS,Z | ; Es este el servo a actualizar?
goto | S_01b | ; No, chequeamos siguiente caso
movf | MensajeIn,W | ; Si, actualizamos su registro
movwf | Posic0
return | ;Regresamos a la espera de una nueva orden
S_01b | movlw | d'1'
xorwf | DispNo,W
btfss | STATUS,Z | ; Es este el servo a actualizar?
goto | S_02b | ; No, chequeamos siguiente caso
movf | MensajeIn,W | ; Si, actualizamos su registro
movwf | Posic1

return | ;Regresamos a la espera de una nueva orden
S_02b | movlw | d'2'
xorwf | DispNo,W
btfss | STATUS,Z | ; Es este el servo a actualizar?
goto | S_03b | ; No, chequeamos siguiente caso
movf | MensajeIn,W | ; Si, actualizamos su registro
movwf | Posic2
return | ;Regresamos a la espera de una nueva orden
S_03b | movlw | d'3'
xorwf | DispNo,W
btfss | STATUS,Z | ; Es este el servo a actualizar?
goto | S_04b | ; No, chequeamos siguiente caso
movf | MensajeIn,W | ; Si, actualizamos su registro
movwf | Posic3
return | ;Regresamos a la espera de una nueva orden
S_04b | movlw | d'4'
xorwf | DispNo,W
btfss | STATUS,Z | ; Es este el servo a actualizar?
goto | S_05b | ; No, chequeamos siguiente caso
movf | MensajeIn,W | ; Si, actualizamos su registro
movwf | Posic4
return | ;Regresamos a la espera de una nueva orden
S_05b | movlw | d'5'
xorwf | DispNo,W
btfss | STATUS,Z | ; Es este el servo a actualizar?
goto | S_06b | ; No, chequeamos siguiente caso
movf | MensajeIn,W | ; Si, actualizamos su registro
movwf | Posic5
return | ;Regresamos a la espera de una nueva orden
S_06b | movlw | d'6'
xorwf | DispNo,W
btfss | STATUS,Z | ; Es este el servo a actualizar?
goto | S_07b | ; No, chequeamos siguiente caso
movf | MensajeIn,W | ; Si, actualizamos su registro
movwf | Posic6
return | ;Regresamos a la espera de una nueva orden
S_07b | movlw | d'7'
xorwf | DispNo,W
btfss | STATUS,Z | ; Es este el servo a actualizar?
goto | S_Errb | ; No, chequeamos siguiente caso
movf | MensajeIn,W | ; Si, actualizamos su registro
movwf | Posic7
return | ;Regresamos a la espera de una nueva orden
S_Errb return | ;Error en numero de servo. No se hace nada

M_Error ;No es un registro conocido o es de solo lectura. Se ignora. Return

;---------------------------------------------------------------------
ReadReg | ;Leemos Registro solicitado por I2C
;---------------------------------------------------------------------
| ;Haremos un Pseudo CASE que lea el registro solicitado y lo deje en MensajeOut
M_04R | ;xxxxxxxxxx Entrada analógica xxxxxxxxxx
movlw | d'4' | ;
xorwf | Registro,W | ;
btfss | STATUS,Z | ; Es este el registro a leer?
goto | M_07R | ; No, chequeamos siguiente caso
; Si. procedemos a leer el registro
A_00 | movlw | d'0'
xorwf | DispNo,W
btfss | STATUS,Z | ; Es este el puerto analógico a leer?
goto | A_01 | ; No, chequeamos siguiente caso
movf | Analog0,W | ; Si. procedemos a leer el registro
movwf | MensajeOut | ; y lo mandamos al master
return | ; Regresamos a la espera de una nueva orden
A_01 | movlw | d'1'
xorwf | DispNo,W
btfss | STATUS,Z | ; Es este el puerto analógico a leer?

goto | A_02 | ; No, chequeamos siguiente caso
movf | Analog1,W | ; Si. procedemos a leer el registro
movwf | MensajeOut | ; y lo mandamos al master
return | ; Regresamos a la espera de una nueva orden
A_02 | movlw | d'2'
xorwf | DispNo,W
btfss | STATUS,Z | ; Es este el puerto analógico a leer?
goto | A_03 | ; No, chequeamos siguiente caso
movf | Analog2,W | ; Si. procedemos a leer el registro
movwf | MensajeOut | ; y lo mandamos al master
return | ; Regresamos a la espera de una nueva orden
A_03 | movlw | d'3'
xorwf | DispNo,W
btfss | STATUS,Z | ; Es este el puerto analógico a leer?
goto | A_04 | ; No, chequeamos siguiente caso
movf | Analog3,W | ; Si. procedemos a leer el registro
movwf | MensajeOut | ; y lo mandamos al master
return | ; Regresamos a la espera de una nueva orden
A_04 | movlw | d'4'
xorwf | DispNo,W
btfss | STATUS,Z | ; Es este el puerto analógico a leer?
goto | A_Error | ; No, chequeamos siguiente caso
movf | Analog4,W | ; Si. procedemos a leer el registro
movwf | MensajeOut | ; y lo mandamos al master
return | ; Regresamos a la espera de una nueva orden

A_Error ;No es un puerto analógico válido. Se devuelve valor 0
clrf MensajeOut
return
M_07R | ;xxxxxxxxxx Version fimware xxxxxxxxxx
movlw | d'7' | ;
xorwf | Registro,W | ;
btfss | STATUS,Z | ; Es este el registro a leer?
goto | M_ErrorR | ; No, chequeamos siguiente caso
movlw | Version | ; Si. procedemos a leer el registro (en este caso una constante)
movwf | MensajeOut
return | ; Regresamos a la espera de una nueva orden
M_ErrorR | ;No es un registro conocido. Se devuelve valor 0
clrf | MensajeOut
return

;---------------------------------------------------------------------------------------ReadAnalog ;Leemos el puerto analógico "APort" y dejamos su valor en "Analog" ;---------------------------------------------------------------------------------------

;Copiamos el numero de puerto a una variable temporal
banksel APort
movf | APort,W
movwf | APortTmp

;Configuración para uso de conversor A/D

banksel ADCON1
movlw | b'00101111' | ;A0,1,2,3,5 Entradas (Analógicas) , A4 Salida (Led)
movwf | TRISA | ;
movlw | b'00000000' | ;Todas las entradas son analógicas. Justif ADRESH
movwf | ADCON1 | ;
banksel ADCON0
movlw | b'11000001' | ;osci interno, activación módulo conversor
bcf | STATUS,C | ;Limpiamos acarreo
rlf | APortTmp,F | ;desplaza a la izda los bits de APortTmp para que los..
rlf | APortTmp,F | ;..3 bits indicadores del puerto estén en la misma posición..
rlf | APortTmp,F | ;..que CHS0...CHS2 de ADCON0...
iorwf | APortTmp,W | ;..Para incluirlos en la configuración de lectura
movwf | ADCON0 | ;
movlw | d'2' | ;Pausa para que de tiempo al condensador interno...
movwf | Pausa | ;..a capturar el valor analógico
call | HacerTiempo

banksel ADCON0
bsf | ADCON0,GO | ;Hace medición de presión

AD_W | btfsc | ADCON0,GO_DONE ;Conversión finalizada?
goto | AD_W | ;No. Seguimos esperando
movf | ADRESH,W | ;Si. Tomamos valor
movwf | Analog
return

;---------------------------------------------------------------------------------------HacerTiempo ;realiza una pausa del numero de centesimas de segundo especificadas en "Pausa" ;El tiempo real es aproximado, dependiendo del número de interrupciones ;que se producan.
;---------------------------------------------------------------------------------------
movf | Pausa,W | ;Coloca el valor de pausa en BDel2...
movwf | BDel2 | ;...para no alterar su contenido
; |
; Generado con PDEL ver SP r 1.0 el 24/02/03 Hs 18:31:22
; Descripcion: Delay 10000 ciclos (1 centésima de segundo)
; |
BCiclo movlw | .8 | ; 1 set numero de repeticion (B)
movwf | BDel0 | ; 1 |
BLoop1 movlw | .249 | ; 1 set numero de repeticion (A)
movwf | BDel1 | ; 1 |
BLoop2 nop | | ; 1 nop
nop | | ; 1 ciclo delay
decfsz | BDel1, 1 ; 1 + (1) es el tiempo 0 ? (A)
goto | BLoop2 | ; 2 no, loop
decfsz | BDel0, 1 ; 1 + (1) es el tiempo 0 ? (B)
goto | BLoop1 | ; 2 no, loop
BDelL1 goto BDelL2 | ; 2 ciclos delay
BDelL2 nop | | ; 1 ciclo delay
; |
decfsz BDel2,F | ;Repite tantas veces el ciclo de una decima de segundo...
goto | BCiclo | ;..como se lo indique BDel2
return | | ; 2+2 Fin.

Fin
END

# Ejemplo de Master

El siguiente sería un ejemplo de montaje electrónico para el Master que controlaría dicho servomotor.

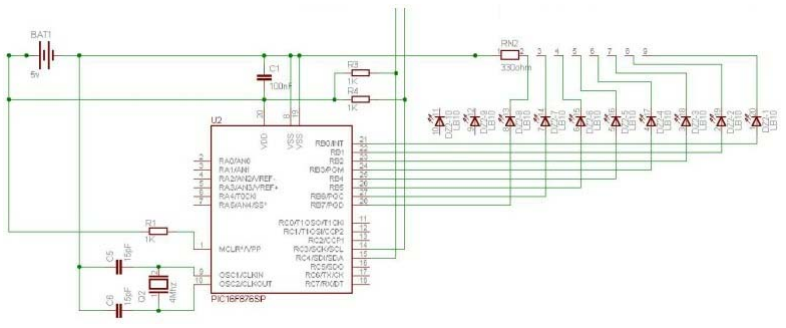
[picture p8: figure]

A continuación se incluye un ejemplo de código para el Master, que de forma cíclica lee la entrada analógica número 0 y muestra su valor digital en la barrera de leds. Asímismo mueve los servos 1 y 6 de un lado a otro, a posiciones concretas. El código para control del Slave ha de incluirse en el cuerpo del programa (donde el bucle MLoop) y

## consiste simplemente en utilizar las rutinas que se han documentado al principio del programa. Se cargan los datos deseados en las variables

indicadas para cada rutina y se llama a la rutina.

## En caso de variar la dirección del slave, será necesario variar la macro #define DirSvI2C

b'01110000'

; msvi-02
; Master para control del módulo SvI2C ; Por: Alejandro Alonso Puig
; Fecha: 11/10/2003
; Controlador: 16F876 4Mhz
; Función:
; Controla por I2C el módulo slave de control de servos y puertos analógicos SvI2C ;
; Las subrutinas definidas para el intercambio de datos con el módulo SvI2C
; son los siguientes:
;
;
; ESCRITURA DE REGISTROS
; ----------------------
;
; SetPosSvI2C | Ordena por i2c al módulo SvI2C la actualización del registro
; | de posición del servo "ServoSvI2C" según el valor de
; | "PosSvI2C".
;
; SetOffsetSvI2C | Ordena por i2c al módulo SvI2C la actualización del registro
; | de Offset del servo "ServoSvI2C" según el valor de
; | "OffsetSvI2C".
;
; SetModoSvI2C | Ordena por i2c al módulo SvI2C la actualización del registro
; | Mode que establece el sentodo de giro de los servos
; | según el valor de "ModoSvI2C".

; LECTURA DE REGISTROS
; ----------------------
;
; ReadVerSvI2C | Obtiene por i2c la versión de firmware del módulo SvI2C
; | y la deja en la variable "VerSvI2C"
;
; ReadAnalogSvI2C | Obtiene por i2c el valor digital (8bits) de la señal analógica
; | presente en el puerto "APortSvI2C" del módulo SvI2C y lo
; | deja en "AnalogSvI2C"
list | p=16F876
include | "P16F876.INC"

;Definición de constantes

#define ClockValue | d'9' | ;(100khz) valor para cálculo de vel. I2C que pasará a SSPADD

#define DirSvI2C | b'01110000' | ;Dirección Módulo SvI2C (01110000)

;Códigos de registro del módulo SvI2C
#define SvI2CModo | d'1' | ;Modo de funcionamiento de servo (normal=0 o reverse=1)

#define SvI2COffset | d'2' | ;Offset

#define SvI2CPos | d'3' | ;Posicion

#define SvI2CAnalog | d'4' | ;Entrada analógica

#define SvI2CVer | d'7' | ;Versión Firmware

;Definición de variables

cblock 0x20
MensajeIn | ;Contendrá el dato recibido por I2C del slave
MensajeOut | ;Contendrá el dato a enviar por I2C al slave
DirSlave | ;Dirección del Slave

BkStatus | ;Backup del registro STATUS
BkW | ;Backup W
BDel0 | ;Usada en retardos
BDel1 | ;Usada en retardos
BDel2 | ;Usada en retardos
Pausa | ;Usada en para hacer pausas con subr "HacerTiempo"

;Dispositivos del módulo SvI2C
ServoSvI2C | ;Servo cuyo registro se accederá por i2c
APortSvI2C | ;Puerto analógico

;Registros del módulo SvI2C
PosSvI2C | ;Posición que se desea que tenga la servo
OffsetSvI2C | ;Offset que se desea que tenga el servo
ModoSvI2C | ;Registro de modo (normal/reverse)
VerSvI2C | ;Versión Firmware
AnalogSvI2C | ;Valor puerto analógico
endc | ;Fin de definiciones
org | 0
goto | INICIO
org | 5

;-------------------------------------------------------------------------------

INICIO | ;Inicio del cuerpo del programa
banksel TRISA | ;Apunta a banco 1
movlw | b'00011111' | ;Entrada (switches). Solo 5 inferiores
movwf | TRISA | ;
movlw | b'00000000' | ;Salida (Leds)
movwf | TRISB | ;
banksel PORTB | ;Apunta a banco 0
clrf | PORTB | ;Limpia puerto B
clrf | PORTA | ;Limpia puerto A
call | init_i2c_Master | ;Configuración para uso de i2c
clrf | MensajeIn
clrf | MensajeOut
movlw | d'10' | ;Pausa de 10 centésimas de segundo para que en...
movwf | Pausa | ;...el arranque de tiempo a los slaves a quedar...
call | HacerTiempo | ;..configurados adecuadamente.
movlw | d'220' | ;posición
movwf | PosSvI2C

MLoop

;Proceso para resetear el slave en caso de bloqueo de algún tipo call Send_RStart
call Send_Stop
banksel PORTB

;lee versión firmware y la muestra por PORTB
; | call | ReadVerSvI2C
; | movf | VerSvI2C,W
; | movwf | PORTB

;Ordena funcionamiento servo 2 y 4 en sentido reverse. Resto normal
; | movlw | b'00010100'
; | movwf | ModoSvI2C

; | call | SetModoSvI2C

;lee valor analógico puerto 0 y la muestra por PORTB
movlw | d'0'
movwf | APortSvI2C
call | ReadAnalogSvI2C
movf | AnalogSvI2C,W
movwf | PORTB

;Ordena movimiento a posición concreta
movlw | d'1' | ;Servo
movwf | ServoSvI2C
movlw | d'10' | ;posición
movwf | PosSvI2C
call | SetPosSvI2C

;pausa de 10 centésimas de segundo
movlw | d'10'
movwf | Pausa
call | HacerTiempo

;Ordena movimiento a posición concreta
movlw | d'6' | ;Servo
movwf | ServoSvI2C
movlw | d'180' | ;posición
movwf | PosSvI2C
call | SetPosSvI2C

;pausa de 10 centésimas de segundo
movlw | d'10'
movwf | Pausa
call | HacerTiempo

;-----Ciclo2-------

;Ordena movimiento a posición concreta
movlw | d'1' | ;Servo
movwf | ServoSvI2C
movlw | d'200' | ;posición
movwf | PosSvI2C
call | SetPosSvI2C

;pausa de 10 centésimas de segundo
movlw | d'10'
movwf | Pausa
call | HacerTiempo

;Ordena movimiento a posición concreta
movlw | d'6' | ;Servo
movwf | ServoSvI2C
movlw | d'10' | ;posición
movwf | PosSvI2C
call | SetPosSvI2C

;pausa de 10 centésimas de segundo
movlw | d'10'
movwf | Pausa
call | HacerTiempo
goto | MLoop

;********************************************************************************* ; SUBRUTINAS
;*********************************************************************************

;-------------------------------------------------------------------------------
SetPosSvI2C | ;Ordena por i2c al módulo SvI2C la actualización del registro
;de posición del servo "ServoSvI2C" según el valor de ;"PosSvI2C".
;-------------------------------------------------------------------------------

banksel DirSlave
movlw | DirSvI2C
movwf | DirSlave
movlw | SvI2CPos | ;Código de registro a acceder
movwf | MensajeOut
call | Send_Start | ;Envía condición de inicio
banksel DirSlave
call | Enviar | ;Envía por I2C dirección de Slave y nº registro
movf | ServoSvI2C,W | ;Se deja el nº de servo en W para que...
call | Send_Byte | ;...Send_Byte lo envíe por i2c
movf | PosSvI2C,W | ;Se deja el valor de posición en W para que...
call | Send_Byte | ;...Send_Byte lo envíe por i2c
call | Send_Stop | ;Envía condición de stop
banksel DirSlave
return

;-------------------------------------------------------------------------------
SetOffsetSvI2C | ;Ordena por i2c al módulo SvI2C la actualización del registro
;de Offset del servo "ServoSvI2C" según el valor de ;"OffsetSvI2C".
;-------------------------------------------------------------------------------

banksel DirSlave
movlw | DirSvI2C
movwf | DirSlave
movlw | SvI2COffset | ;Código de registro a acceder
movwf | MensajeOut
call | Send_Start | ;Envía condición de inicio
banksel DirSlave
call | Enviar | ;Envía por I2C dirección de Slave y nº registro
movf | ServoSvI2C,W | ;Se deja el nº de servo en W para que...
call | Send_Byte | ;...Send_Byte lo envíe por i2c
movf | OffsetSvI2C,W ;Se deja el valor de Offset en W para que...
call | Send_Byte | ;...Send_Byte lo envíe por i2c
call | Send_Stop | ;Envía condición de stop
banksel DirSlave
return

;-------------------------------------------------------------------------------
SetModoSvI2C | ;Ordena por i2c al módulo SvI2C la actualización del registro
;Mode que establece el sentodo de giro de los servos ;según el valor de "ModoSvI2C". ;-------------------------------------------------------------------------------

banksel DirSlave
movlw | DirSvI2C
movwf | DirSlave
movlw | SvI2CModo | ;Código de registro a acceder
movwf | MensajeOut
call | Send_Start | ;Envía condición de inicio
banksel DirSlave
call | Enviar | ;Envía por I2C dirección de Slave y nº registro
movlw | d'0' | ;Se deja cualquier valor de nºDispositivo porque..
call | Send_Byte | ;...este dato no es tomado en cuenta por Slave
movf | ModoSvI2C,W | ;Se deja el valor de Offset en W para que...
call | Send_Byte | ;...Send_Byte lo envíe por i2c
call | Send_Stop | ;Envía condición de stop
banksel DirSlave
return

;-------------------------------------------------------------------------------
ReadVerSvI2C | ;Obtiene por i2c la versión de firmware del módulo SvI2C
;y la deja en la variable "VerSvI2C" ;-------------------------------------------------------------------------------

banksel DirSlave
movlw | DirSvI2C
movwf | DirSlave
movlw | SvI2CVer | ;Código de registro a acceder
movwf | MensajeOut
call | Send_Start | ;Envía condición de inicio
banksel DirSlave
call | Enviar | ;Envía por I2C dirección de Slave y nº registro
movlw | d'0' | ;Se deja cualquier valor de nºDispositivo porque..
call | Send_Byte | ;...este dato no es tomado en cuenta por Slave
call | Send_RStart | ;Envía condición de reinicio
banksel DirSlave
call | Recibir | ;Toma dato del Slave...
movf | MensajeIn,W | ;...y lo guarda en...
movwf | VerSvI2C | ;...la variable de registro correspondiente
call | Send_Stop | ;Envía condición de stop
banksel DirSlave

return

;-------------------------------------------------------------------------------
ReadAnalogSvI2C | ;Obtiene por i2c el valor digital (8bits) de la señal analógica
;presente en el puerto "APortSvI2C" del módulo SvI2C y lo ;deja en "AnalogSvI2C"
;-------------------------------------------------------------------------------

banksel DirSlave
movlw | DirSvI2C
movwf | DirSlave
movlw | SvI2CAnalog | ;Código de registro a acceder
movwf | MensajeOut
call | Send_Start | ;Envía condición de inicio
banksel DirSlave
call | Enviar | ;Envía por I2C dirección de Slave y nº registro
movf | APortSvI2C,W | ;Se envía el número de puerto analógico..
call | Send_Byte | ;...a leer del slave
call | Send_RStart | ;Envía condición de reinicio
banksel DirSlave
call | Recibir | ;Toma dato del Slave...
movf | MensajeIn,W | ;...y lo guarda en...
movwf | AnalogSvI2C | ;...la variable de registro correspondiente
call | Send_Stop | ;Envía condición de stop
banksel DirSlave

return

;-------------------------------------------------------------------------------
init_i2c_Master | ;Inicializa valores para uso de I2C en Master
;Ha de ser llamado tras definir TRISC y un valor para ;ClockValue. Para frecuencia SCL=Fosc/(4x(ClockValue+1)) ;-------------------------------------------------------------------------------

;Guardamos copia de algunos registros
movwf | BkW | ;Hace copia de W
movf | STATUS,W | ;Hace copia de registro de estado
banksel PORTA
movwf BkStatus

;Configuramos I2C
banksel TRISC | ; Pasamos a direccionar Banco 1
movlw | b'00011000' | ; Establece líneas SDA y SCL como entradas...
iorwf | TRISC,f | ;..respetando los valores para otras líneas.
movlw | ClockValue | ; Establece velocidad I2C segun...
movwf | SSPADD | ; ...valor de ClockValue
bcf | SSPSTAT,6 | ; Establece I2C input levels
bcf | SSPSTAT,7 | ; Habilita slew rate
banksel SSPCON | ; Pasamos a direccionar Banco 0
movlw | b'00111000' | ; Master mode, SSP enable, velocidad segun...
movwf | SSPCON | ; ... Fosc/(4x(SSPADD+1))
bcf | PIR1,SSPIF | ; Limpia flag de eventos SSP
bcf | PIR1,7 | ; Limpia bit. Mandatorio por Datasheet

;Restauramos las copias de los registros
movf | BkStatus,W | ;Restaura las copias de registros
movwf | STATUS | ;registro de estado
movf | BkW,W | ;registro W

return

; --------------------------------------------------------------------------------------Enviar ;Envía un mensaje (comando) almacenado en "MensajeOut" al Slave cuya dirección ;se ha de encontrarse en la variable "DirSlave" ;---------------------------------------------------------------------------------------

;Guardamos copia de algunos registros
movwf | BkW | ;Hace copia de W
movf | STATUS,W | ;Hace copia de registro de estado
banksel PORTA
movwf BkStatus

StEnv
banksel DirSlave
movf | DirSlave,W | ;Dirección esclavo
call | Send_Byte | ;Envía dirección y orden de escritura
call | WrtAckTest | ;Verifica llegada ACK
banksel SSPCON2
bcf | SSPCON2,ACKSTAT | ;limpia flag ACK
xorlw | 1
btfss | STATUS,Z | ;Chequea si llegó ACK
goto | SigueEnv | ;Si. Seguimos con envío dato
call | Send_Stop | ;No. Reintentamos envío
call | Send_Start
goto | StEnv

SigueEnv
banksel MensajeOut
movf | MensajeOut,W | ;Lo deja en W para que la subrutina Send_Byte lo envíe
call | Send_Byte | ;envía por i2c

;Restauramos las copias de los registros
movf | BkStatus,W | ;Restaura las copias de registros
movwf | STATUS | ;registro de estado
movf | BkW,W | ;registro W

return

; --------------------------------------------------------------------------------------Recibir ;Solicita dato al Slave cuya dirección ha de encontrarse en la variable ;"DirSlave" y lo mete en "MensajeIn". ;---------------------------------------------------------------------------------------

;Guardamos copia de algunos registros
movwf | BkW | ;Hace copia de W
movf | STATUS,W | ;Hace copia de registro de estado
banksel PORTA
movwf BkStatus

StRec
banksel DirSlave
movf | DirSlave,W | ;Dirección esclavo
iorlw | b'00000001' | ;con orden de lectura
call | Send_Byte | ;Envía dirección y orden de lectura
call | WrtAckTest | ;Verifica llegada ACK
banksel SSPCON2
bcf | SSPCON2,ACKSTAT | ;limpia flag ACK
xorlw | 1
btfsc | STATUS,Z | ;Chequea si llegó ACK
goto | StRec | ;No. Reintentamos envío
;Si. Leemos dato
call | Rec_Byte | ;Recibe dato por i2c y lo mete en "MensajeIn"

;Restauramos las copias de los registros
movf | BkStatus,W | ;Restaura las copias de registros

movwf | STATUS | ;registro de estado
movf | BkW,W | ;registro W

return

; --------------------------------------------------------------------------------------Send_Start ;Envía condición de start ;---------------------------------------------------------------------------------------

banksel SSPCON2
bsf | SSPCON2,SEN | ; Envía Start
call | CheckIdle | ;Espera fin evento
return

; --------------------------------------------------------------------------------------Send_RStart ;Envía condición de Repeated Start ;---------------------------------------------------------------------------------------

banksel SSPCON2
bsf | SSPCON2,RSEN | ; Envía Repeated Start
call | CheckIdle | ;Espera fin evento
return

; --------------------------------------------------------------------------------------
Send_Ack | ;Envía Ack
;---------------------------------------------------------------------------------------

banksel SSPCON2
bcf | SSPCON2,ACKDT ; acknowledge bit state to send (ack)
bsf | SSPCON2,ACKEN ; Inicia secuencia de ack
call | CheckIdle | ;Espera fin evento
return

; --------------------------------------------------------------------------------------
Send_Nack | ;Envía Nack para finalizar recepción
;---------------------------------------------------------------------------------------

banksel SSPCON2
bsf | SSPCON2,ACKDT ; acknowledge bit state to send (not ack)
bsf | SSPCON2,ACKEN ; Inicia secuencia de nack
call | CheckIdle | ;Espera fin evento
return

; --------------------------------------------------------------------------------------
Send_Stop | ;Envía condición de stop
;---------------------------------------------------------------------------------------

banksel SSPCON2
bsf | SSPCON2,PEN | ;Activa secuencia de stop
call | CheckIdle | ;Espera fin evento
return

; --------------------------------------------------------------------------------------
Send_Byte | ;Envía el contenido de W por i2c
;---------------------------------------------------------------------------------------
banksel SSPBUF | ; Cambia a banco 0
movwf | SSPBUF | ; inicia condicion de escritura
call | CheckIdle | ;Espera fin evento
return

; --------------------------------------------------------------------------------------
Rec_Byte | ;Recibe dato por i2c y lo mete en "MensajeIn"
;---------------------------------------------------------------------------------------
banksel SSPCON2 | ; Cambia a banco 1
bsf | SSPCON2,RCEN | ; genera receive condition

btfsc | SSPCON2,RCEN | ; espera a que llegue el dato
goto | $-1
banksel SSPBUF | ; Cambia a banco 0
movf | SSPBUF,w | ; Mueve el dato recibido ...
movwf | MensajeIn | ; ... a MensajeIn
call | CheckIdle | ;Espera fin evento
return

; --------------------------------------------------------------------------------------
CheckIdle | ;Chequea que la operación anterior termino y se puede proceder con
;el siguiente evento SSP
;---------------------------------------------------------------------------------------
banksel SSPSTAT | ; Cambia a banco 1
btfsc | SSPSTAT, R_W | ; Transmisión en progreso?
goto | $-1
movf | SSPCON2,W
andlw | 0x1F | ; Chequeamos con mascara para ver si evento en progreso
btfss | STATUS, Z
goto | $-3 | ; Sigue en progreso o bus ocupado. esperamos
banksel PIR1 | ; Cambia a banco 0
bcf | PIR1,SSPIF | ; Limpiamos flag
return

;---------------------------------------------------------------------------------------WrtAckTest ;Chequea ack tras envío de dirección o dato
;Devuelve en W 0 o 1 dependiendo de si llegó (0) o no (1) ACK ;---------------------------------------------------------------------------------------
banksel SSPCON2 | ; Cambia a banco 1
btfss | SSPCON2,ACKSTAT ;Chequea llegada ACK desde slave
retlw | 0 | ;llegó ACK
retlw | 1 | ;no llegó ACK

;---------------------------------------------------------------------------------------HacerTiempo ;realiza una pausa del numero de centesimas de segundo especificadas en "Pausa"

;---------------------------------------------------------------------------------------

movf | Pausa,W | ;Coloca el valor de pausa en BDel2...
movwf | BDel2 | ;...para no alterar su contenido
; |
; Generado con PDEL ver SP r 1.0 el 24/02/03 Hs 18:31:22
; Descripcion: Delay 10000 ciclos (1 centésima de segundo)
; |
BCiclo movlw | .8 | ; 1 set numero de repeticion (B)
movwf | BDel0 | ; 1 |
BLoop1 movlw | .249 | ; 1 set numero de repeticion (A)
movwf | BDel1 | ; 1 |
BLoop2 nop | | ; 1 nop
nop | | ; 1 ciclo delay
decfsz | BDel1, 1 ; 1 + (1) es el tiempo 0 ? (A)
goto | BLoop2 | ; 2 no, loop
decfsz | BDel0, 1 ; 1 + (1) es el tiempo 0 ? (B)
goto | BLoop1 | ; 2 no, loop
BDelL1 goto BDelL2 | ; 2 ciclos delay
BDelL2 nop | | ; 1 ciclo delay
; |
decfsz BDel2,F | ;Repite tantas veces el ciclo de una decima de segundo...
goto | BCiclo | ;..como se lo indique ADel2
return | | ; 2+2 Fin.

END
